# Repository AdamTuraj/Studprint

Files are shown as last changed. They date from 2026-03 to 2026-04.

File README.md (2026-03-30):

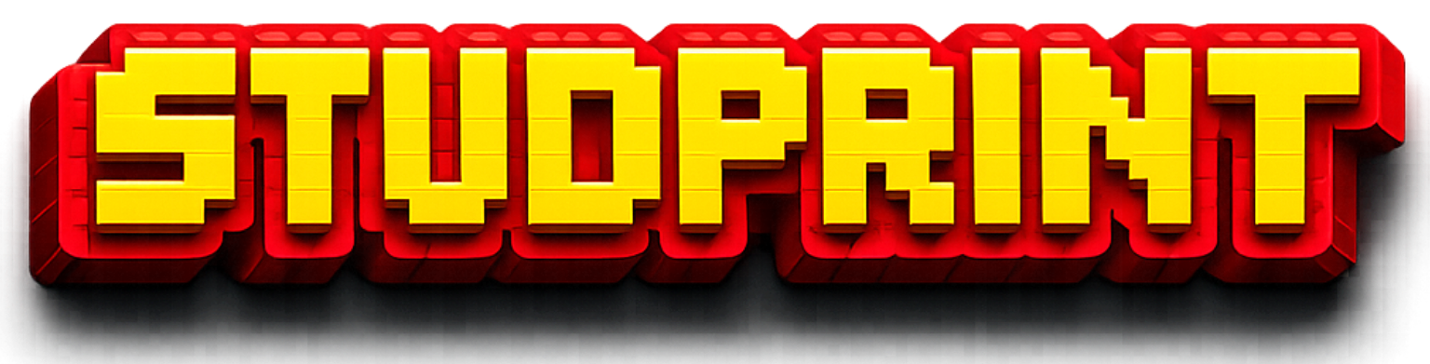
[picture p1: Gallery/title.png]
Studprint
## 

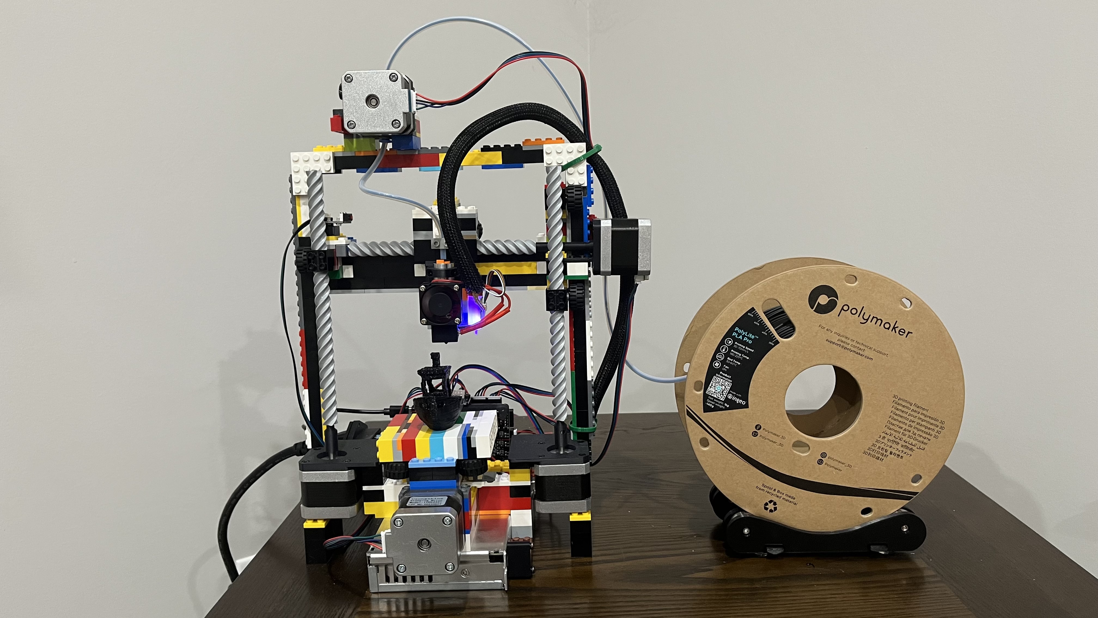
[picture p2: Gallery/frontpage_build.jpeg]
Picture of the build


**A standard bedslinger...but with a twist! The frame, motion system, and extruder are made out of 92%[^1] LEGO bricks.**

## About

This project started as a response to a Hack Club YSWS called [Infill](https://infill.hackclub.com). The challenge was to build a 3D printer for under $350, with a twist. Having grown up with LEGO, I decided to make the entire printer out of it.

To make this printer truly one of a kind, I took it a step further: not only would it be built from LEGO, but I would also use only classical LEGO bricks[^2] wherever possible. As you might expect, some parts, especially the custom mounts for steppers, electronics, and other hardware, can't realistically be made under that limitation.

[^1]: Calculated by taking the number of LEGO components and dividing by the total number of components reported in the BOM within the SolidWorks drawings

[^2]: I defined classical LEGO as the bricks and parts that interface with them (i.e., no Technic)

## Cost

LEGO cost will vary depending on local availability, and the BOM cost is only a rough estimate. Prices in the sheet reflect the time it was created and are not guaranteed to stay the same. Some parts may also go out of stock, since this BOM will not be actively maintained.

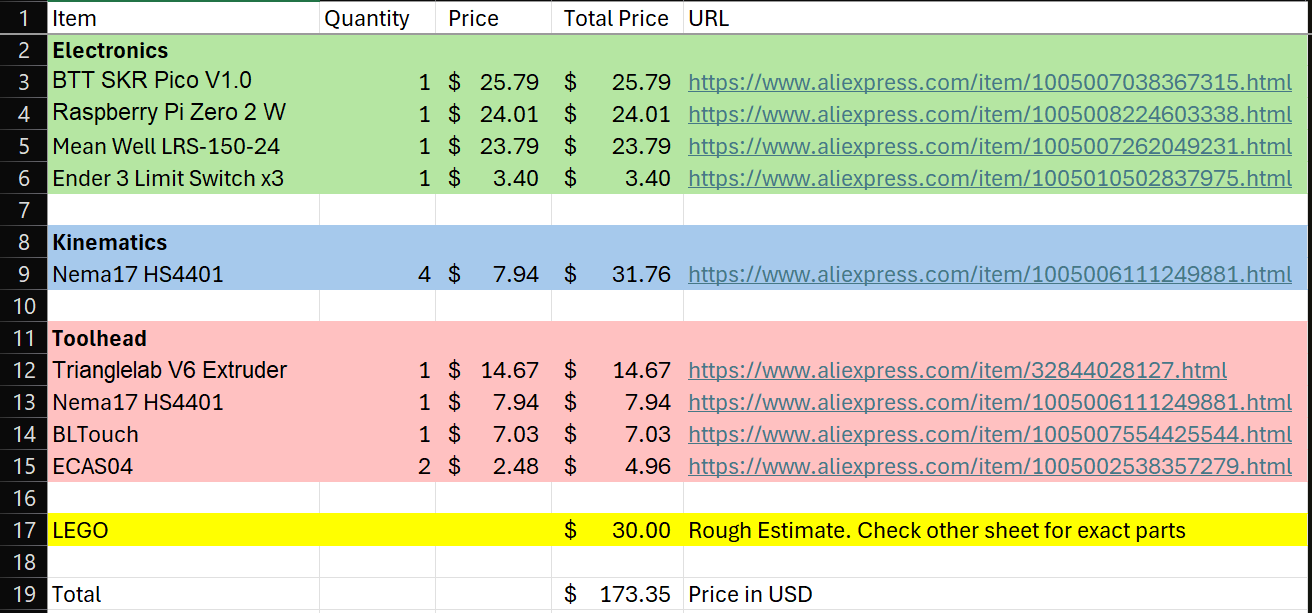
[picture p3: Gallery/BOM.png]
BOM


## License

StudPrint is licensed under the CERN Open Hardware Licence. See the full license text in [LICENSE](LICENSE).

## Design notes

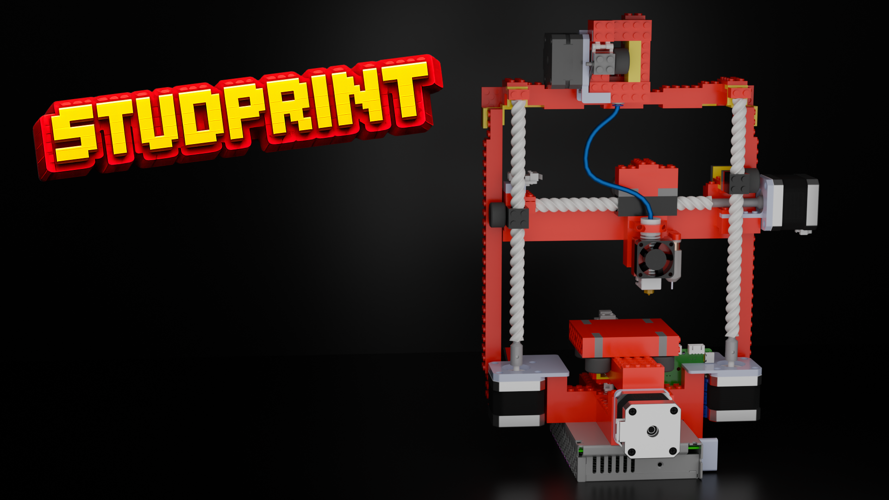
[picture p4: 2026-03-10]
Gallery/frontpage.png

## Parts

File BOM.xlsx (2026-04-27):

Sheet: Off the shelf parts
Item | Quantity | Price | Total Price | URL | Notes
Electronics
BTT SKR Pico V1.0 | 1 | $25.79 | $25.79 | https://www.aliexpress.com/item/1005007038367315.html
Raspberry Pi Zero 2 W | 1 | $15.00 | $15.00 | https://www.raspberrypi.com/products/raspberry-pi-zero-2-w/
Mean Well LRS-150-24 | 1 | $23.79 | $23.79 | https://www.aliexpress.com/item/1005007262049231.html
Ender 3 Limit Switch | 1 | $3.40 | $3.40 | https://www.aliexpress.com/item/1005010502837975.html | Get the pack of 3
Kinematics
Nema17 HS4401 | 4 | $7.94 | $31.76 | https://www.aliexpress.com/item/1005006111249881.html
Toolhead
Trianglelab V6 Extruder | 1 | $14.67 | $14.67 | https://www.aliexpress.com/item/32844028127.html
Nema17 HS4401 | 1 | $7.94 | $7.94 | https://www.aliexpress.com/item/1005006111249881.html
BLTouch | 1 | $7.03 | $7.03 | https://www.aliexpress.com/item/1005007554425544.html
ECAS04 | 2 | $2.48 | $4.96 | https://www.aliexpress.com/item/1005002538357279.html
Sherpa Mini Extruder Parts | 1 | $2.48 | $2.48 | https://www.aliexpress.com/item/1005006023988927.html | Only the drive gears and thumbscrew assembly is needed
LEGO |  |  | $60.00 | Rough Estimate. Check other sheet for exact parts
Total |  |  | $196.82 | Price in USD before tax and shipping

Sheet: LEGO
ITEM NO. | PART NUMBER | QTY. | Bricklink URL
1 | lego2x6_red | 48 | https://www.bricklink.com/catalogItem.asp?P=2456
2 | legop2x16_red | 2 | https://www.bricklink.com/catalogItem.asp?P=4282
3 | legop1x2_red | 29 | https://www.bricklink.com/catalogItem.asp?P=3023
4 | legop2x2_red | 29 | https://www.bricklink.com/catalogItem.asp?P=3022
5 | legop2x4_red | 35 | https://www.bricklink.com/catalogItem.asp?P=3020
6 | Brick with Hole for Worm Screw 6L | 6 | https://www.bricklink.com/catalogItem.asp?P=73764
7 | legop2x3_red | 15 | https://www.bricklink.com/catalogItem.asp?P=3021
8 | 1x2_2x2_bracket | 25 | https://www.bricklink.com/catalogItem.asp?P=44728
9 | lego1x2_red | 14 | https://www.bricklink.com/catalogItem.asp?P=3004
10 | wheel_connector | 15 | https://www.bricklink.com/catalogItem.asp?P=4488
11 | lego_wheel | 15 | https://www.bricklink.com/catalogItem.asp?P=55981
12 | lego2x3_red | 14 | https://www.bricklink.com/catalogItem.asp?P=3002
13 | lego2x2_red | 6 | https://www.bricklink.com/catalogItem.asp?P=3003
14 | lego2x4_red | 41 | https://www.bricklink.com/catalogItem.asp?P=3001
15 | legop1x4_red | 3 | https://www.bricklink.com/catalogItem.asp?P=3710
16 | legop2x6_red | 38 | https://www.bricklink.com/catalogItem.asp?P=3795
17 | legop2x8_red | 1 | https://www.bricklink.com/catalogItem.asp?P=3034
18 | lego1x2_hole | 4 | https://www.bricklink.com/catalogItem.asp?P=3700
19 | Technic Worm Gear 6L | 11 | https://www.bricklink.com/catalogItem.asp?P=73763
20 | Technic Axle Pin | 2 | https://www.bricklink.com/catalogItem.asp?P=43093
21 | lego1x6_red | 2 | https://www.bricklink.com/catalogItem.asp?P=3009
22 | lego1x4_red | 1 | https://www.bricklink.com/catalogItem.asp?P=3010
23 | plate_4x4_corner | 5 | https://www.bricklink.com/catalogItem.asp?P=2639
24 | legop_1x2_2_clips | 1 | https://www.bricklink.com/catalogItem.asp?P=60470
25 | legop_1x2_handle | 1 | https://www.bricklink.com/catalogItem.asp?P=48336
 | Total LEGOs: | 363

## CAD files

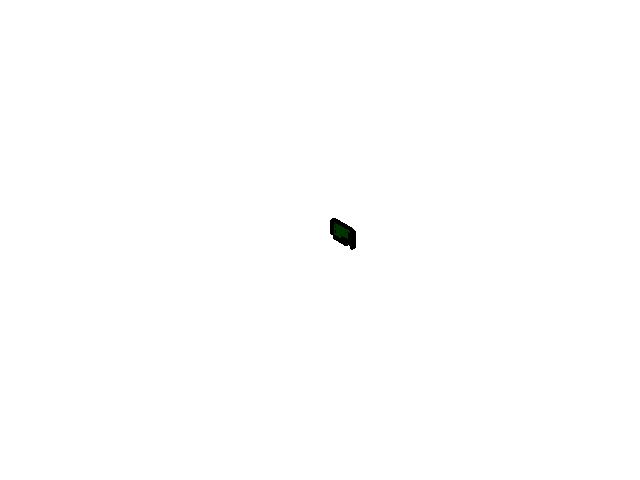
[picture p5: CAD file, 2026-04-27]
CAD/External Parts/BTT SKR Pico/BTT SKR Pico V1.0.SLDASM
LOGO_-1
XH2.54-5P_H-2
LOGO_-3 x 4
XH2.54-3P-4 x 4
USB_Type-C_A-13
LOGO_0.5
XH2.54-2P-19
LOGO_-20
LOGO_-21 x 4
XH2.54-3P_H-22 x 4
LOGO_-25 x 6
KF301-26 x 6
LOGO_-27 x 5
XH2.54-4P_H-28 x 5
LOGO_-36 x 5
XH2.54-2P_H-37 x 5

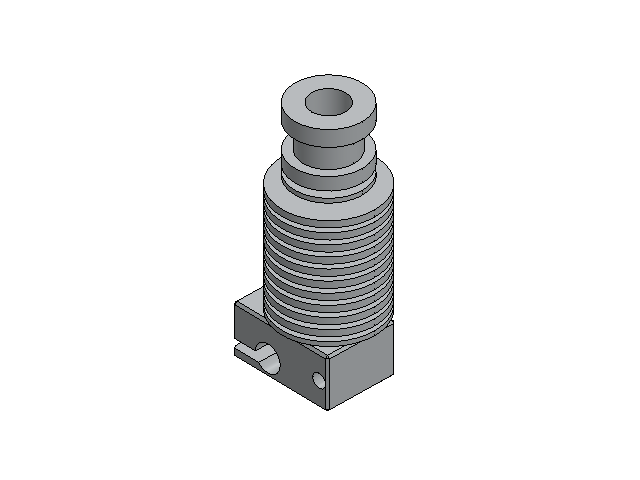
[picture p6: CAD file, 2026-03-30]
CAD/External Parts/E3D_V6/E3D_V6.SLDASM
E3D_v6_Heat sink
E3D_v6_Heat break
E3D_V6_Heater block
E3D_v6_nozzle0.4mm

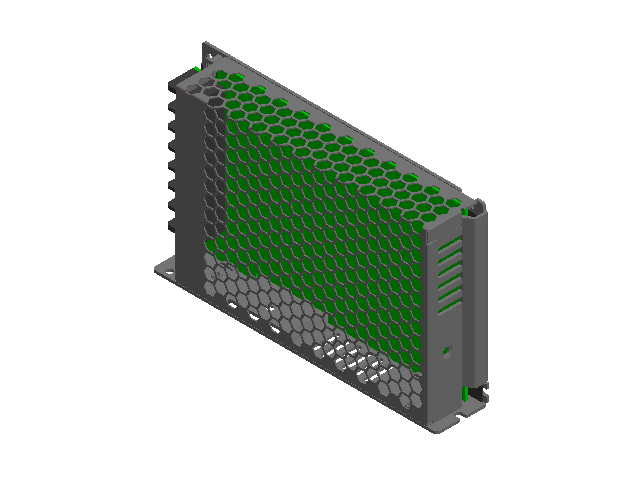
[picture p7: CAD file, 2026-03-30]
CAD/External Parts/PSU/LRS-150-24.SLDASM


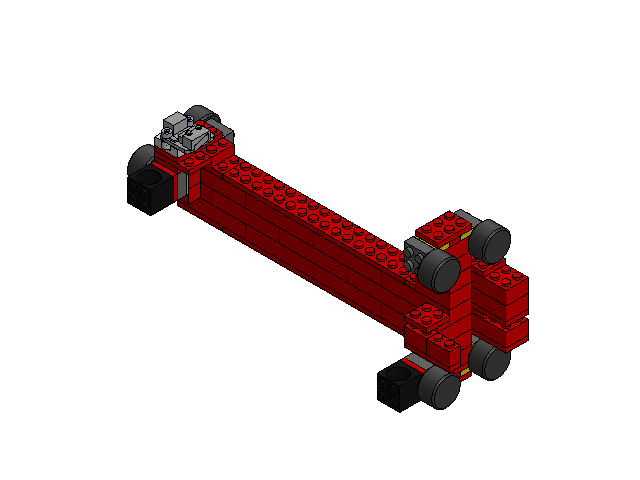
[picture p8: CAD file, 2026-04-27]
CAD/X Rail.SLDASM
lego2x6_red x 12
legop2x16_red x 2
legop1x2_red x 9
legop2x2_red x 6
legop2x4_red x 5
Brick with Hole for Worm Screw 6L x 2
legop2x3_red x 5
1x2_2x2_bracket x 6
lego1x2_red x 6
wheel_connector x 6
lego_wheel x 6
lego2x3_red x 8
Limit Switch
Limit Switch Mount
lego2x2_red
lego2x4_red
legop1x4_red
M3x4mm Heatset x 2
M3x6mm x 2

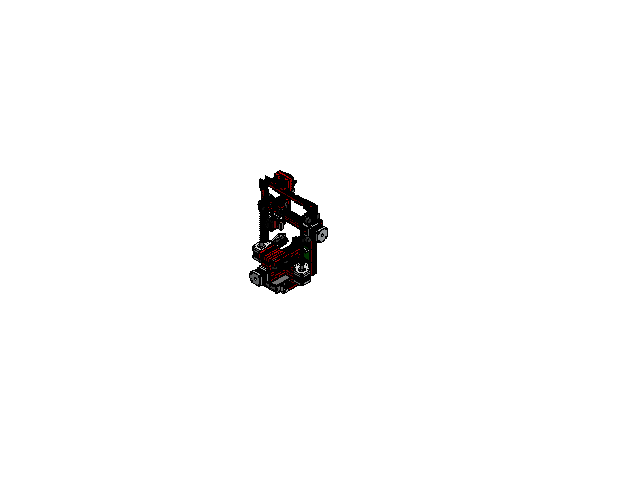
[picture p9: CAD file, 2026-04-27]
CAD/StudPrint.SLDASM
lego2x6_red x 48
legop2x16_red x 2
legop1x2_red x 29
legop2x2_red x 29
legop2x4_red x 35
Brick with Hole for Worm Screw 6L x 6
legop2x3_red x 15
1x2_2x2_bracket x 25
lego1x2_red x 14
wheel_connector x 15
lego_wheel x 15
lego2x3_red x 14
Limit Switch x 2
Limit Switch Mount
lego2x2_red x 6
lego2x4_red x 41
legop1x4_red x 3
M3x4mm Heatset x 7
M3x6mm x 4
E3D_v6_Heat sink
E3D_v6_Heat break
E3D_V6_Heater block
E3D_v6_nozzle0.4mm
Hotend Mount
BL-touch
BLTouch Mount
3010 Radial Fan
TriangleLabs Shroad
legop2x6_red x 38
legop2x8_red
lego1x2_hole x 4
M3_Hex_Nut x 2
M3x12mm x 2
Nema 17 x 4
Technic Axle Pin x 2
X Stepper Axle Adapter
X Stepper Mount
Technic Worm Gear 6L x 11
M3x8mm x 22
Stepper Axle Mount x 3
Y Axis Stepper Mount
Limit Mount
lego1x6_red x 2
lego1x4_red
Power Switch Mount
Stepper Mount Z Left
Stepper Mount Z Right
plate_4x4_corner x 5
Nema 17 Stepper (42-34)
Primary gear 1.75-5.0
P6SS_Setscrew_ISO 4026 - M3 x 2-N
Idler Connector
Secondary gear 1.75-5.0_without_setscrew
stift 3x20
needlebearing x 2
Plunger (1) x 2
Collet Body (1) x 2
Seal Retainer (1) x 2
Grab Ring (1) x 2
legop_1x2_2_clips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

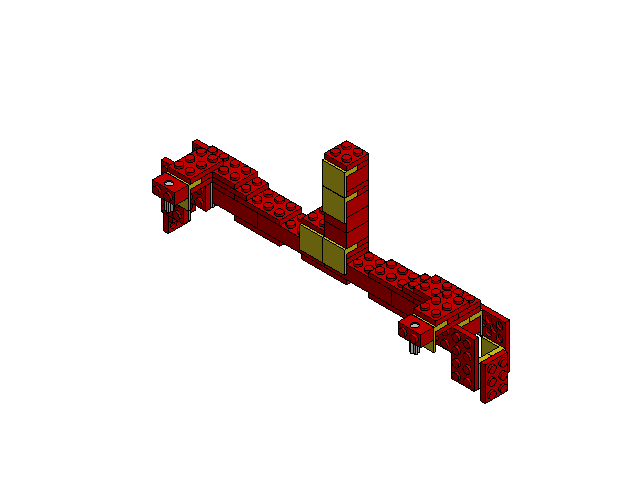
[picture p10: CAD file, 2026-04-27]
CAD/Z Axis Top Connector.SLDASM
lego2x6_red x 4
legop2x4_red x 8
1x2_2x2_bracket x 10
plate_4x4_corner x 4
legop1x2_red x 3
legop2x3_red x 2
legop2x2_red x 5
lego2x2_red x 2
legop2x6_red

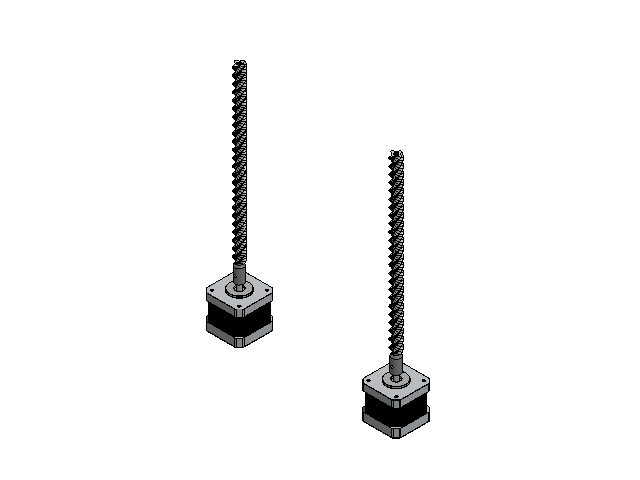
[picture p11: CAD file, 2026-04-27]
CAD/Z Axis Motion.SLDASM
Technic Worm Gear 6L x 6
Stepper Axle Mount x 2
Nema 17 x 2

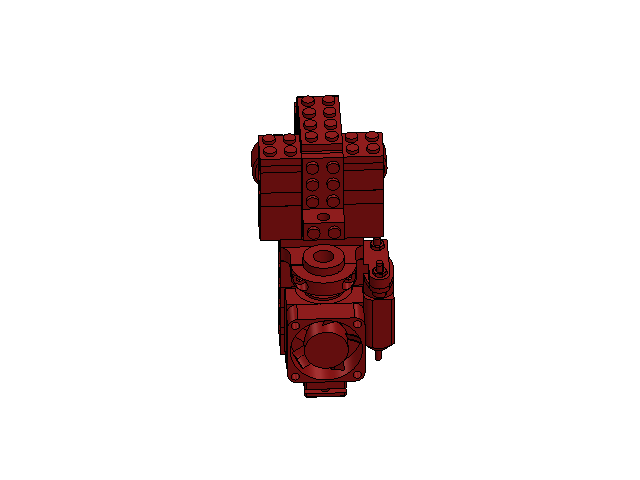
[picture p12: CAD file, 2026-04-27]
CAD/Toolhead.SLDASM
E3D_v6_Heat sink
E3D_v6_Heat break
E3D_V6_Heater block
E3D_v6_nozzle0.4mm
Hotend Mount
BL-touch
BLTouch Mount
3010 Radial Fan
TriangleLabs Shroad
lego_wheel x 5
wheel_connector x 5
lego2x4_red x 2
lego1x2_red x 2
legop2x2_red x 7
legop2x4_red x 7
lego2x6_red
legop2x6_red
Brick with Hole for Worm Screw 6L x 3
1x2_2x2_bracket x 3
lego2x2_red x 2
legop2x8_red
lego1x2_hole
M3x4mm Heatset x 2
M3x6mm x 2
M3_Hex_Nut x 2
M3x12mm x 2

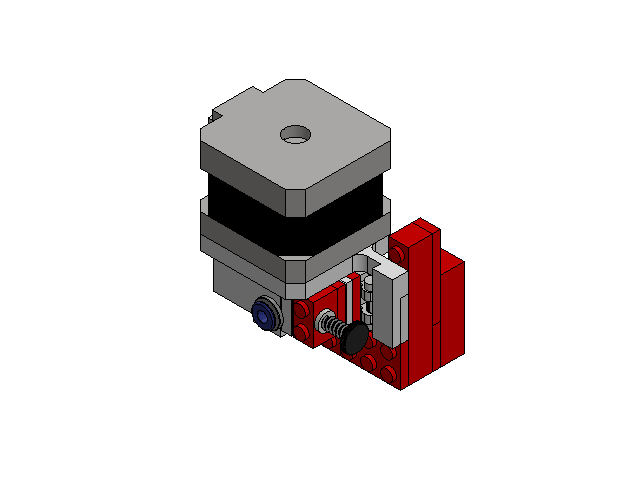
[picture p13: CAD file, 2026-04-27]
CAD/Extruder.SLDASM
Nema 17 Stepper (42-34)
Primary gear 1.75-5.0
P6SS_Setscrew_ISO 4026 - M3 x 2-N
Idler Connector
Secondary gear 1.75-5.0_without_setscrew
stift 3x20
needlebearing x 2
Plunger (1) x 2
Collet Body (1) x 2
Seal Retainer (1) x 2
Grab Ring (1) x 2
legop1x2_red x 2
legop_1x2_2_clips
legop_1x2_handle
lego1x6_red
lego2x6_red
lego2x2_red
legop2x3_red x 2
legop2x2_red
plate_4x4_corner
lego1x2_red
lego1x2_hole
lego2x4_red x 2
legop1x4_red
ECAS Exit Mount
ECAS Entrance Mount
Extruder Stepper Mount
M3x8mm x 4
M3 washer - nylon
Thumbscrew
spring
M3x4mm Heatset

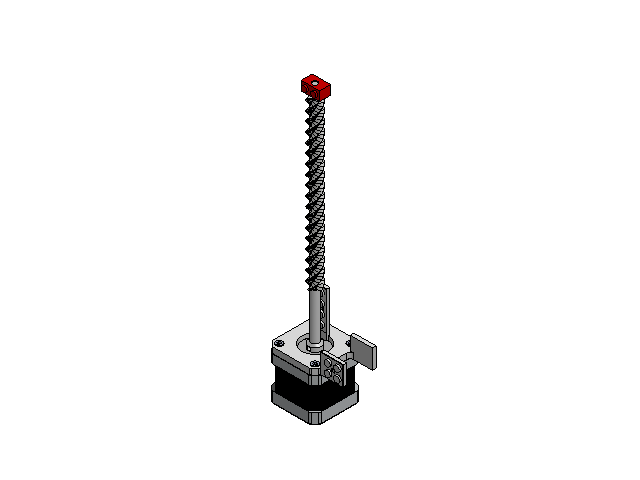
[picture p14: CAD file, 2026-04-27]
CAD/X Motion.SLDASM
Nema 17
Technic Axle Pin
lego1x2_hole
X Stepper Axle Adapter
X Stepper Mount
Technic Worm Gear 6L x 3
M3x8mm x 4

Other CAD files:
CAD/External Parts/ECAS04/ecas04.SLDASM
CAD/External Parts/Power Rocker Switch/Power Rocker Switch.SLDASM
CAD/External Parts/BTT SKR Pico/XH2.54-5P_H.SLDASM
CAD/External Parts/Drivegear/Primary.SLDASM
CAD/External Parts/BTT SKR Pico/Board.SLDASM
CAD/External Parts/BTT SKR Pico/P11.SLDASM
CAD/External Parts/Drivegear/Idler Gear.SLDASM
CAD/External Parts/BTT SKR Pico/U9.SLDASM
CAD/Custom Parts/BLTouch Mount.SLDPRT
CAD/Custom Parts/BTT Mount.SLDPRT
CAD/Custom Parts/ECAS Entrance Mount.SLDPRT
CAD/Custom Parts/ECAS Exit Mount.SLDPRT
CAD/Custom Parts/Extruder Stepper Mount.SLDPRT
CAD/Custom Parts/Hotend Mount.SLDPRT
CAD/Custom Parts/Idler Connector.SLDPRT
CAD/Custom Parts/Left PSU Mount.SLDPRT
CAD/Custom Parts/Limit Mount.SLDPRT
CAD/Custom Parts/Limit Switch Mount.SLDPRT
CAD/Custom Parts/Power Switch Mount.SLDPRT
CAD/Custom Parts/Right PSU Mount.SLDPRT
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

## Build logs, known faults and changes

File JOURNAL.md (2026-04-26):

# StudPrint Journal

Back at it this year. This is the journal for Infill V2!

### Day 1 (February 13th)

Hours Worked: 2 hours
Total Hours Worked: 2 hours

---

#### BOM Selection

Began choosing the components for this printer. Since it will be a very barebones printer, the BOM is fairly short. You may be confused on why there is no extruder. I am going to try to use LEGO parts and a rubber band as an idler 😅. The BOM can be found in this repo as [BOM.xlsx](/BOM.xlsx). An image of the current version is also below.

BOM

### Day 13 (February 26th)

Hours Worked: 15 hours
Total Hours Worked: 17 hours

---

#### X axis

I haven't been journalling as I should but the X axis has been completed. It is almost all LEGO with the exception of the mounts for the hotend, BLTouch, and the leadscrew adapter. The motion is controlled via LEGO worm screws. Technically they are technique parts but theres no way to get around it. Originally, I wasn't planning on using LEGO for the motion platform but here we are. Below is an image of the X axis:

X axis

#### Y axis

I have also finished the Y axis. It is simply a single linear rod with a LEGO leadscrew. I am a little concerned with the up play but I believe that may not be an issue. Next up is the Z axis, extruder, and electronics, and final touches. Hopefully I can finish it within a week!

Y Axis

### Day 14 (February 27th)

Hours Worked: 2.5 hours
Total Hours Worked: 19.5 hours

---

#### Z axis

The Z axis screw on the left side has been added and I created a mounted solution between that, a linear rail, and the X axis. It was tricky to package it all together nicely; however, it worked out really well in the end. The other side will be slightly trickier but I can apply the same strategies and overall design as the left side.

#### Future Plan

I put together an overall plan I can hopefully follow to finish the preliminary design this week:

**Saturday** I need to finish the other side, add the rails, and connect the Z axis to the Y axis.

**Sunday** I connect the sides together at the top and create the extruder.

**Monday** I make the electronics enclosure. Hopefully by Tuesday / Wednesday I have a BOM ready and can go through my LEGO and pick out all the parts so I can figure out what I need to order.

Here is what that section looks like and the overall look of the printer:
The XZ mount
The printer

### Day 16 (March 1st)

Hours Worked: 1.5 hours
Total Hours Worked: 21 hours

---

#### Z axis

Everything took longer than expected so the schedule above is in the trash. I finished the left side Z axis mount and I am working on the right side. For looks purposes, I want the rails on both sides to be mirrored which is causing issues with the X motion system. Currently playing around with placement until something works.

Z Axis

### Day 18 (March 3rd)

Hours Worked: 4 hours
Total Hours Worked: 25 hours

---

#### XZ Axis

After much consideration, I decided that mounting the X stepper after the Z rail and using a 3D printed part to connect to the worm gear. Not ideal, I was hoping to minimize the 3D printed part use here but due to time constraints and self-imposed visual requirements, I deemed this good enough.

I followed this by designing a mount for the X motor which took a few tries due to the limited space. I did a quick check to ensure there are no collisions and called this part of the Z axis complete. All that is left to do is:

- Connect the left and right Z axis' at the top
- Design the extruder
- Mount the electronics somewhere

I am hoping to finish it by the end of the week!

Close up of XZ on right
Isometric view

### Day 20 (March 5th)

Hours Worked: 6 hours
Total Hours Worked: 31 hours

---

#### Z Axis Top

The Z axis has been finished. I'm a little worried that the top won't be stiff enough. I will hope that its enough and if it isn't I'll try to improve until it works. Unfortunately, it is difficult to stiffen it up more due to lack of space and the limitations of LEGO. Below is a screenshot of this assembly.

XZ Axis

#### Extruder

The final major motion part of this project is complete: the extruder. Using a rubber band to provide tension for the idler and a stepper connected directly to the drive wheel, I can only hope this can provide a consistent enough extrusion. It still needs the adapter between the stepper and wheel; however, thats a later issue. Mounting for the extruder is on the top of the Z axis and is connected accross 4 points. This will hopefully be enough to keep it in place.

Extruder
Complete printer

### Day 21 (March 7th)

Hours Worked: 5 hours
Total Hours Worked: 36 hours

---

#### Electronics

The last part of the project was electronics. Im using the LRS-150 and BTT SKR Pico v1.0. I decided to put the PSU under the printer and mounted the BTT on the back. It looks good and compact. The mounts are not the greatest but they are good enough. My main goal is to get an initial draft done so I can order the parts and get building.

Overall, the initial design is done. I just have to update the BOP and see what parts I need.

Finished printer

#### BOM

I updated the BOM and added the LEGO parts. I still need to figure out the part numbers for the wheel and axle, along with checking how many of the right angle pieces are inverted. Afterwards, I will go through my stash and see what I need!

BOM

### Day 22 (March 11th)

Hours Worked: 0.25 hours
Total Hours Worked: 36.25 hours

---

#### Extruder

I quickly modelled out the axle adapter for the extruder. Due to lack of space, it will be using a friction fit and I may add a blob of glue to ensure it stays. Im not entirely sure if the axle will fit. Its difficult to measure the part I have due to how small it is.

Axle adapter

### Day 23 (March 15th)

Hours Worked: 3 hours
Total Hours Worked: 39.25 hours

---

#### Beginning the build

Day one of the build came with great success. Only two major changes were needed: the Z axis -> top connector, and the Y axis leadscrew mounting on the bed. The custom parts are in the process in being printed and the wormscrews were just shipped. I may completly build it and wait for the wormscrews or 3D print some temporary wormscrews. Below is a picture of the current state of the build.

Build day 1

### Finale (March 16th until April 19th)

Total Worked: 20 hours
Total Hours Worked: 59.25

---

#### Continuing the build

The X axis and stepper mounting went fairly smooth. Some adjustments were made the the X axis mount, along with the buffing up the X axis with the addition of two wheels.
XZ Wheel change

Y axis largely remained the same with the exception of reinforcements to the YZ mounts and the addition of long plates across the bottom to reduce failure.

The Z axis was assembled with minimal issues; only additional reinforcements on the other side of the Z structure along with the removal of top constraints for the Z screws.

The toolhead also had a bit of an upgrade. It had too much rotational play so an additional wheel was added at the bottom of the X rail to mitigate this.
Toolhead change

Finally, the extruder needed a whole redesign. The wheels could not grip the filament well enough so friction from the bowden and hotend caused extrusion to be impossible.

To mitigate this, I decided to ditch the LEGO wheel concept and switched to using BMG dual extruder gears and a springed tensioner. It still utilized LEGO parts; however, it was just unrealistic to use LEGO wheels and expect consistent extrusion.
New extruder

#### Printing!

With all these changes and the printer being fully built, I got printing. After setting up Klipper, I was able to load filament, and successfully print a Benchy boat in about 1.25 hours!
First successful Benchy
The built printer

#### Last minute changes

During RMRRF, I was having consistent issues with the extruder regarding kinking of the bowden tube and a bad filament path. After hearing feedback from others, I decided to rotate the extruder 90 degrees which allows more room for the bowden to compress. This would be the final change to the printer!

Updated motor mount

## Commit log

2026-02-13 Add BOM + JOURNAL
    [BOM.xlsx]
2026-02-27 Day 14 - Forgot to journal
    [1x2_2x2_bracket.SLDPRT, 3010 Radial Fan.SLDPRT, BL-touch.SLDPRT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]
2026-02-28 Day 14.5 - Begin Z axis
    [Limit Switch Mount.SLDPRT, StudPrint.SLDASM, X Motion.SLDASM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]
2026-03-03 Day 15
    [Limit Switch Mount.SLDPRT, Stepper Axel Mount.SLDPRT, Stepper Mount Z.SLDPRT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]
2026-03-03 Day 18
    [Stepper Axel Mount.SLDPRT, Stepper Mount Z Left.SLDPRT, Stepper Mount Z Right.SLDPRT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]
2026-03-06 Day 20
    [625ZZ_001.SLDPRT, Axis.SLDPRT, Bottom.SLDPRT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]
2026-03-08 Day 21
    [0603-15.SLDPRT, 0603.SLDASM, 5558720272.SLDPRT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]
2026-03-10 Update BOM, clean up file structure, add init blender files
    [BOM.xlsx, Board.SLDASM, E3D_V6.SLDASM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]
2026-03-10 Update README and LICENSE
    [Power Rocker Switch.SLDASM]
2026-03-11 Day 22 - Add axle adapter
    [BLTouch Mount.SLDPRT, Board.SLDASM, E3D_V6.SLDASM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]
2026-03-16 Day 23 (build day #1)
    [Board.SLDASM, Bottom Right BTT.SLDPRT, E3D_V6.SLDASM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]
2026-03-22 Pre-toolhead redesign
    [BLTouch Mount.SLDPRT, ECAS04 Mount.SLDPRT, Extruder.SLDASM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]
2026-03-30 She prints!
    [625ZZ_001.SLDPRT, Axis.SLDPRT, BLTouch Mount.SLDPRT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]
2026-04-27 Finalize BOM, add RMRRF build improvements, add fasteners to CAD
    [BOM.xlsx, BTT Mount.SLDPRT, BTT SKR Pico V1.0.SLDASM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]
